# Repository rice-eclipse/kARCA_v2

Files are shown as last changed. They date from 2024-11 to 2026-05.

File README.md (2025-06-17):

# kARCA 2.0
kARCA 2.0 is a revision of [kARCA](https://github.com/rice-eclipse/karca):  Rice Eclipse's Engine Control System PCB for the data collection and remote control 
of their Titan II and Proxima Hybrid Rocket Motors

It performs the same functions as kARCA with the addition of thermocouple data collection, driver current monitoring, and battery monitoring.
In addition, various components have been replaced for updated ICs and the power regulation and load cell circuits have been revised.

A detailed description of the changes can be found on  [karca_v2/Docs/changelog](https://github.com/rice-eclipse/kARCA_v2/blob/main/karca_v2/Docs/kARCA_v2_Changelog.csv)

Detailed documentation on the circuit board can be found on [karca_v2/Docs/main_documentation](https://github.com/rice-eclipse/kARCA_v2/tree/main/karca_v2/Docs/karca_v2.md)

## Download and Usage
Download [KiCAD](https://www.kicad.org/download/)

Navigate to your preferred folder and clone into the repository:
```
git clone https://github.com/rice-eclipse/kARCA_v2.git
```
Open KiCAD and open the project file (.kicad_pro):
```
File > Open Project
```

Schematics: [karca_v2/Docs/Schematics](https://github.com/rice-eclipse/kARCA_v2/tree/main/karca_v2/Docs/Schematics)

Spice Simulations: [karca_v2/Docs/Simulations](https://github.com/rice-eclipse/kARCA_v2/tree/main/karca_v2/Docs/Simulations)

Board Files: [karca_v2/Docs/Board_Files](https://github.com/rice-eclipse/kARCA_v2/tree/main/karca_v2/Docs/Board_Files)

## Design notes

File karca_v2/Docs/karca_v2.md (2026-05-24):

# kARCA 2.0 Main Documentation

This document highlights the features and design choices of kARCA 2.0 as a reference for future work on the project.

## Project Overview
kARCA 2.0 is an engine control system  that is part of Rice Eclipse's Engine Testing Setup. The controller interfaces directly with the engine through the [controller software](https://github.com/rice-eclipse/mc-firmware), which runs on an STM32F207 nucleo board. The user interfaces with the controller using a frontend JavaScript dashboard `Quonkboard` from which they can visualize the data collected and send commands to actuate valves and start the ignition sequence.

**For future versions, it is recommended to upgrade to an STM32F429 for more RAM and a hardware FPU for efficient FIR filtering. The user can also use the STM32F407VET6 if a fully integrated solution is preferred (ie: MCU embedded on the main PCB)**
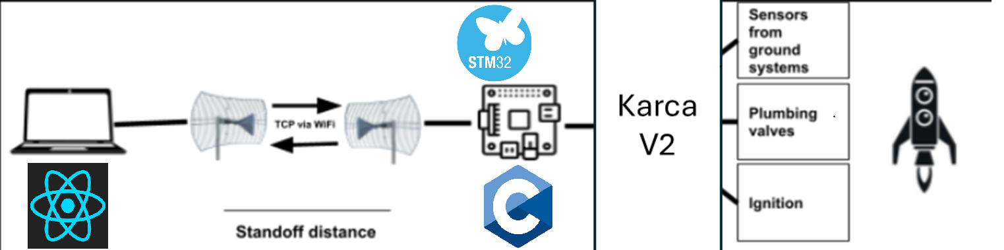
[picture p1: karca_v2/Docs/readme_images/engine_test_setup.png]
Engine Test Setup


## System Requirements
1. Collect data from 4 load cells, pressure transducers, and thermocouples at a 1kHz samplingfrequency
2. Control the 600W ignition system by driving an external two-stage relay
3. Control 5 valves, each drawing up to 1A of current at 12V
4. Monitor Battery voltage and current
5. Transmit real time data to the user

## Design Outline

### Power Distribution

The main power source is a 12V Lead-Acid Battery, which is spliit into 5V and 12V lines.

The 12V line is used for the drivers, ignition circuitry, and the pressure transducers.

The 5V line is used for the remaining ciruitry. The power conversion is performed by the [AP62300](https://www.diodes.com/assets/Datasheets/AP62300_AP62301_AP62300T.pdf) synchronous buck converter.

The battery current is monitored using a current shunt and a current sense amplifier. The voltage is monitored using a simple resistive divider circuit.

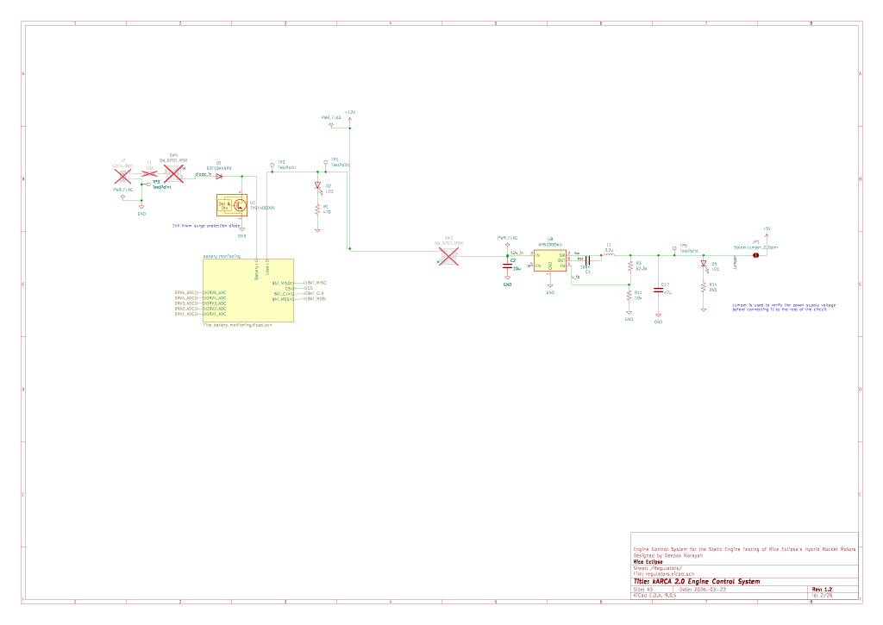
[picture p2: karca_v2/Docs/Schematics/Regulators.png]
Power Regulation

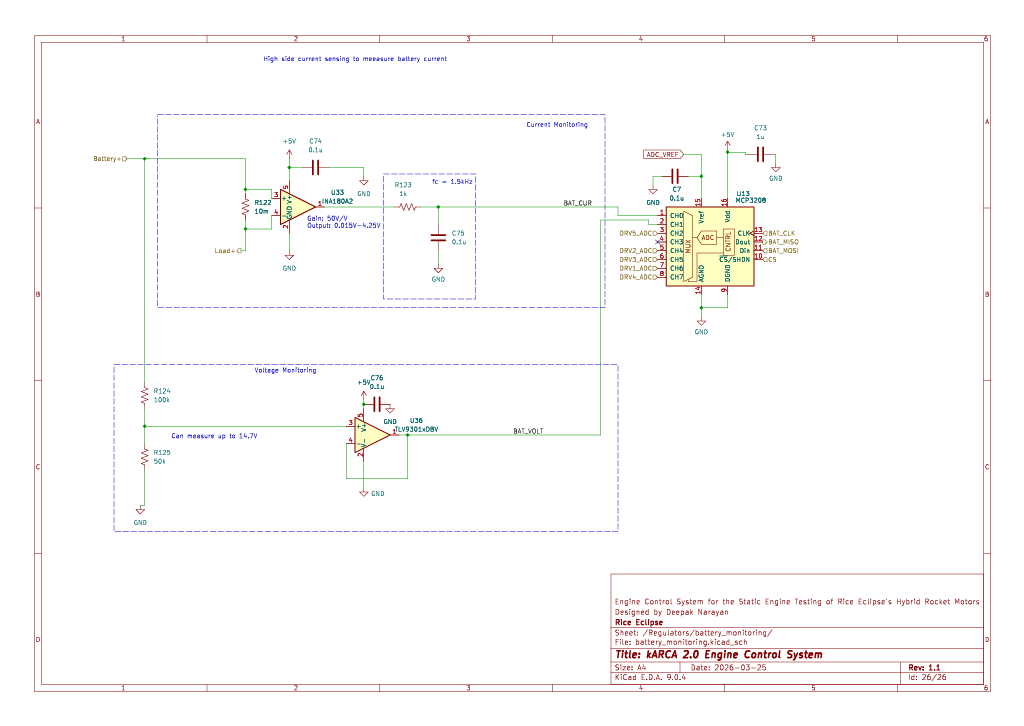
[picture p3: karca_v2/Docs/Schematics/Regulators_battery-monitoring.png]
Battery Monitoring


### Load Cell Data Collection
When supplied with an excitation voltage of 5V, the cell outputs a differential voltage proportonal to the applied force:
$$V_{dm} = \frac{V_{FSO}}{F_{FSO}}V_{DD}F$$
Where:
1. $V_{dm}$ is the output differential voltage
2. $V_{FSO}$ is the load cell's full scale voltage output: 3mV per volt of excitation when 3000lbf is applied
3. $V_{DD}$ is the exccitation voltage(5V in this case)
4. $F$ is the applied force

$V_{dm}$ is amplified using an instrumentation amplifier to obtain a single-ended readable signal (compatible with the ADC voltage resolution of 1.22mV). A two-pin jumper can be used to select the gain resistor connected to the instrumentation amplifier. A gain of 250 for the Titan load cell or a gain of 17 for the Proxima load cell can be chosen.

The single-ended signal is then filtered using a unity-gain active filter with a cutoff frequency of $1.5kHz$. This is to prevent aliasing during sampling.
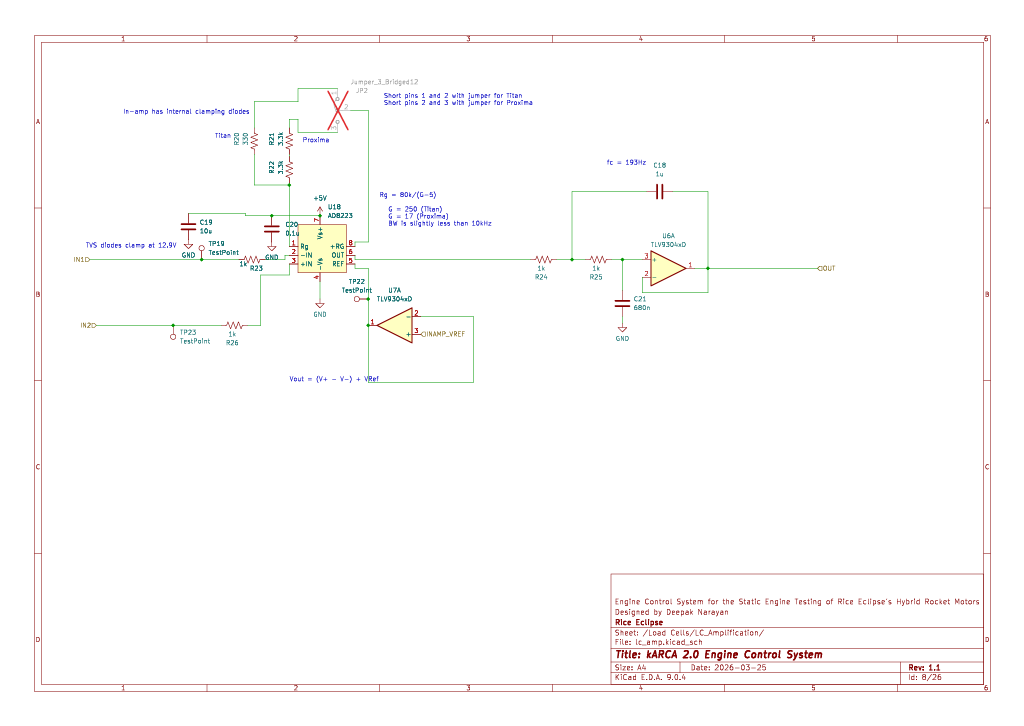
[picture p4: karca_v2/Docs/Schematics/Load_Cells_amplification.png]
Load Cell Amplification


### Pressure Transducer Data Collection
A pressure transducer is a 4-20mA device. It outputs a current that varies linearly with the measured pressure (4mA corresponds to 0 psig; 20mA corresponds to 1000psig). It usually consists of a wheatstone bridge circuit like a load cell and a current loop transmitter that converts the voltage to a current. The current signal provides stronger noise immunity. 

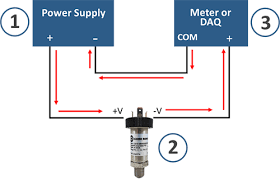
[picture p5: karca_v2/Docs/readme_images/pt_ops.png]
Pressure transducer circuit

The signal is converted back to a voltage using a $30\Omega$ shunt resistor. This results in a voltage range of 0.12V to 0.6V. A low shunt resistance is necessary to minimize the voltage drop as the pressure transducers need a minimum of 8V to operate.

The signal is amplified with a gain of 8 using an active filter with a cutoff frequency of $193Hz$. Therefore the full voltage range is from 0.96V to 4.8V, corresponding to a resolution of 0.31psi.

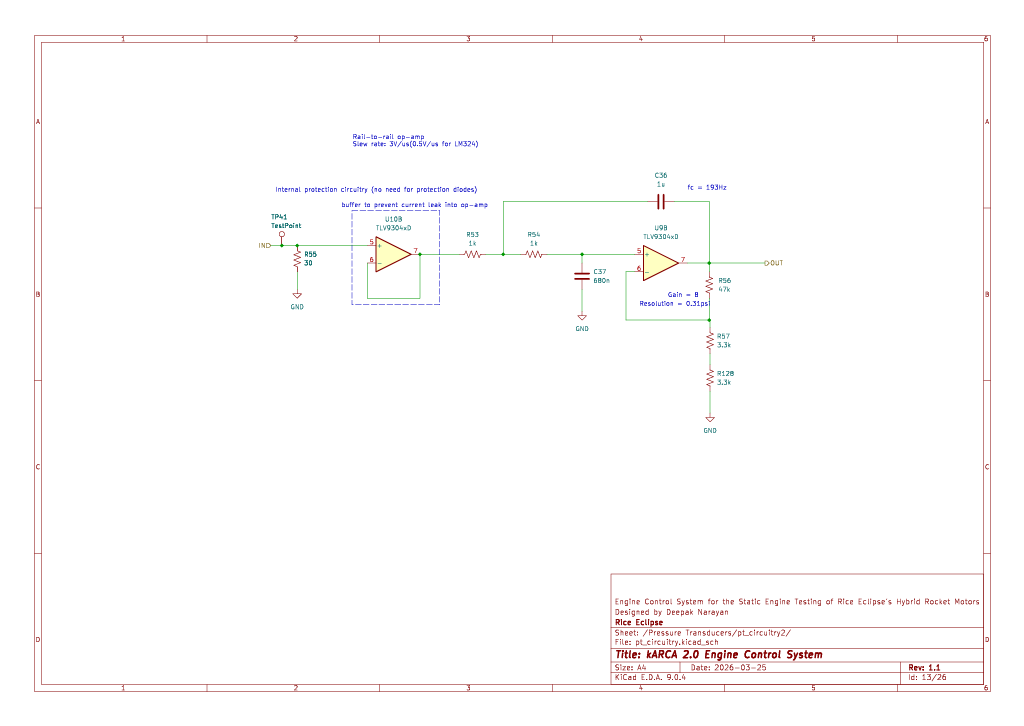
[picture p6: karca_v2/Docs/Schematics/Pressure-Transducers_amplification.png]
Pressure Transducer Amplification


### Thermocouple Data Collection
Thermocouples output a very small voltage signal that is proportional to the temperature difference between the measurement junction and a reference junction.
 ($5mV/^{\\circ}C$). This differential signal is amplified by the AD8495 Thermocouple amplifier with a gain of 122.4. The output voltage is thus:
 $$V_{out} = (T_{measured}\cdot mV/^{\\circ}C)\cdot 122.4$$

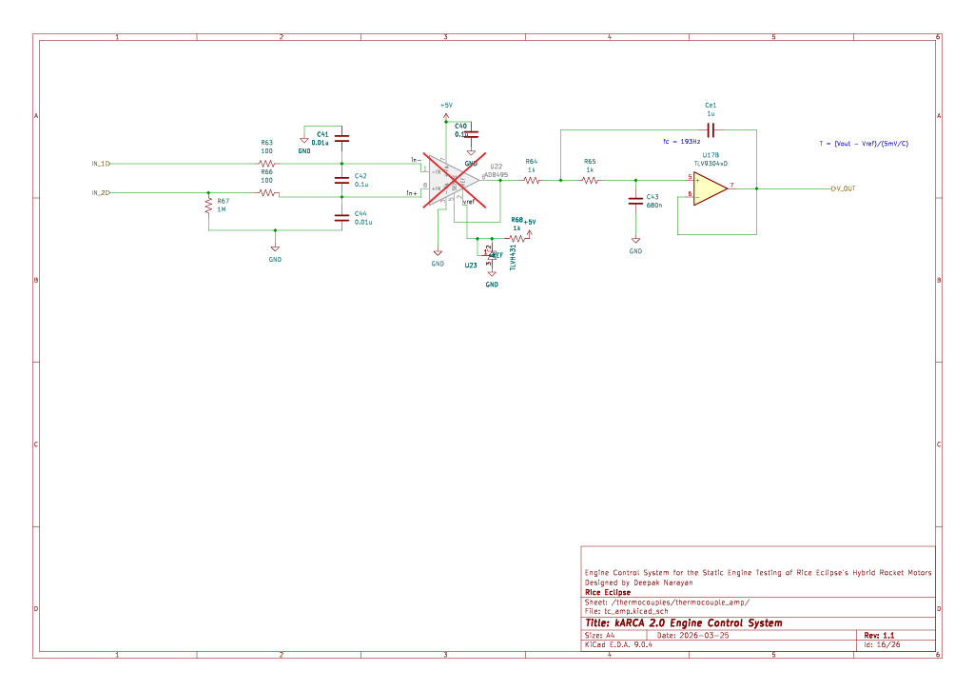
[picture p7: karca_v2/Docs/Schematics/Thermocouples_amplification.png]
Thermocouple Amplification
 

### Analog-to-Digital Conversion and Processing
The analog signals from the thermocouple, load cell, and pressure transducer conditioning circuits are input to two [MCP3208](https://www.microchip.com/en-us/product/mcp3208) 12-bit ADCs. The driver current and battery monitoring circuit outputs are input to a third MCP3208 ADC. The outputs from the first two ADCs are sent to the microcontroller over an SPI bus. The output from the third ADC is sent to the microcontroller over another SPI bus. This allows for a faster sample rate as there are fewer channel scans needed for each sampling cycle.

These ADCs have a Signal to Noise and Distortion (SINAD) of 72dB, providing an ENOB of ~11.

**For future revisions, it is recommended to use the internal ADCs as these allow for easy channel scanning and DMA transactions**
 ### Valve Actuation
 Each valve is driven by the AO3400 mosfet. These mosfets have a very low $$R_{DS,on}$$, allowing sufficient current to flow when then gate is driven by 3.3V from the 
 STM32F207 GPIO. There are also green status LEDs that light up, when a valve is actuated.

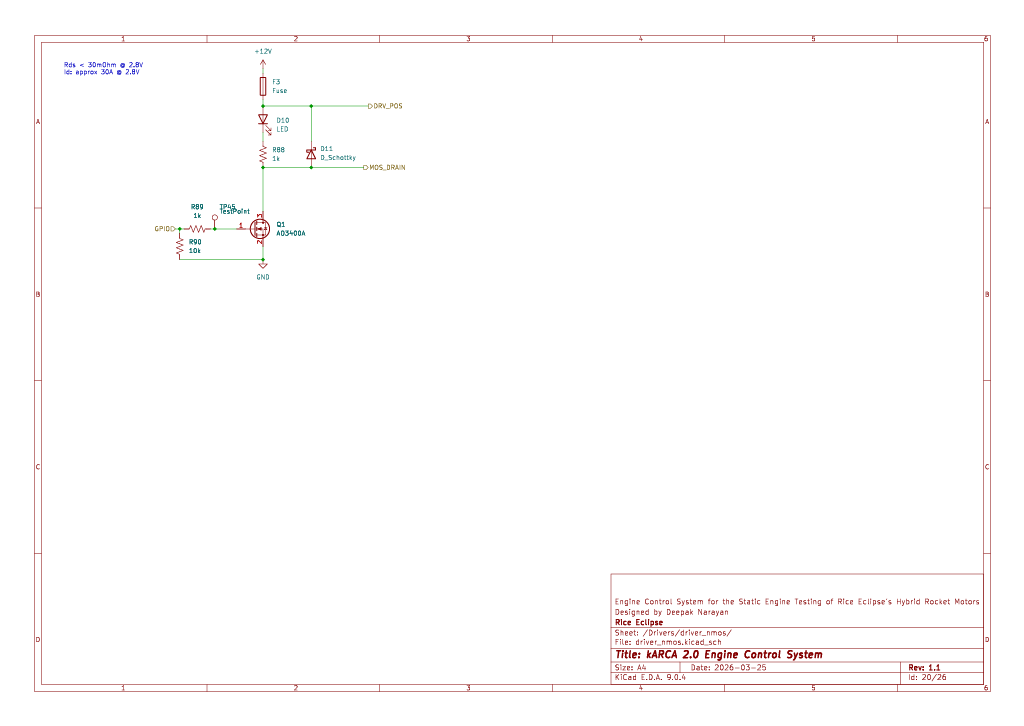
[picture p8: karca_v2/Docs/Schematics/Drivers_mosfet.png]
Driver Schematics
 

 To ensure that the valve actuates when the driver is turned on, the current through the valve is measured using current sense amplifiers and shunt resistors.
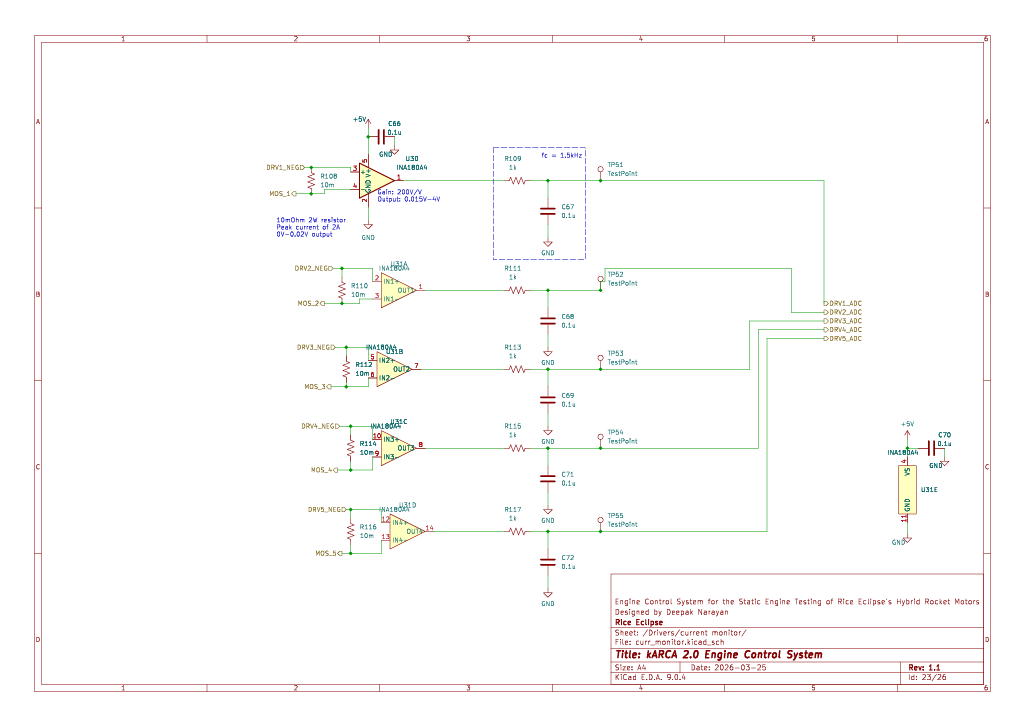
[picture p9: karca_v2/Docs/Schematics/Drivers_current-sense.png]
Driver Current Sense
 

 ### Board Layout
 The board is 25cm x 14.5cm since space wasn't a major concern. Components were grouped according to their function and were spaced out since being able to modify traces and easily replace components by hand were priorities.

 The board consists of 4 layers: SIGNAL-GND-PWR-SIGNAL. This keeps the signal traces close to a reference plane. The power plane is much simpler than that of the original kARCA design; it only consists of a single 5V plane and the 12V is supplied using traces. This prevents potential signal deterioration due to signals crossing split power planes.

 All the components are mounted on the top layer.

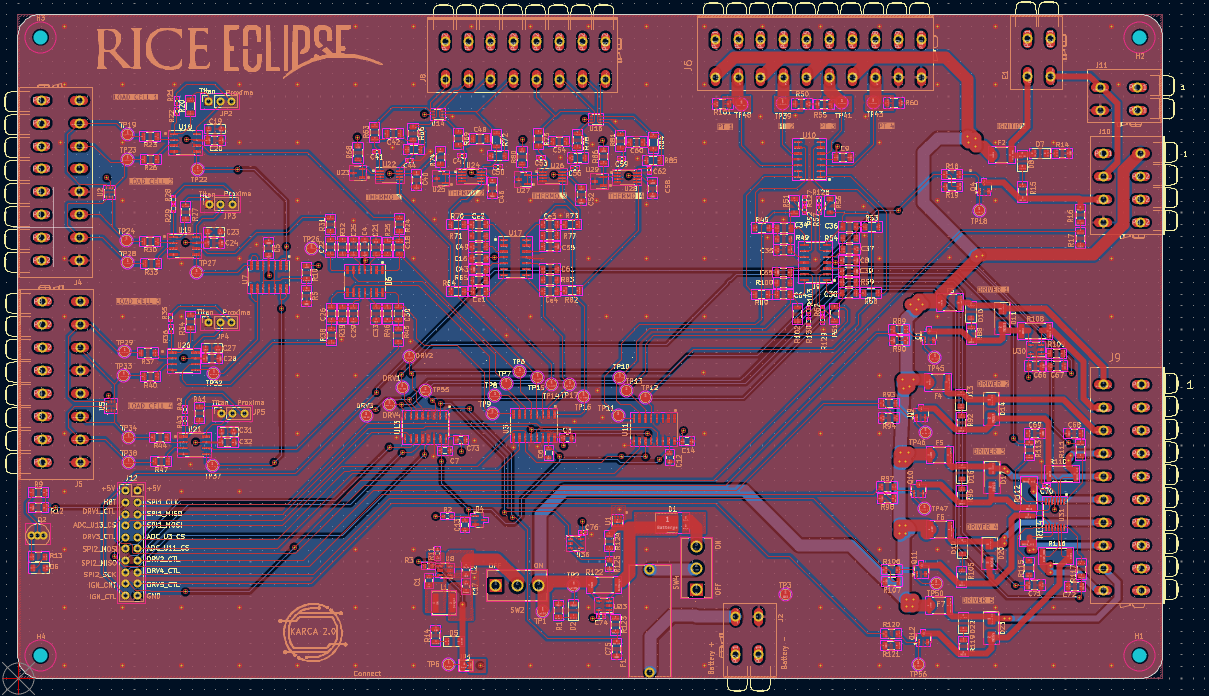
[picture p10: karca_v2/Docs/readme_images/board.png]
Karca
 
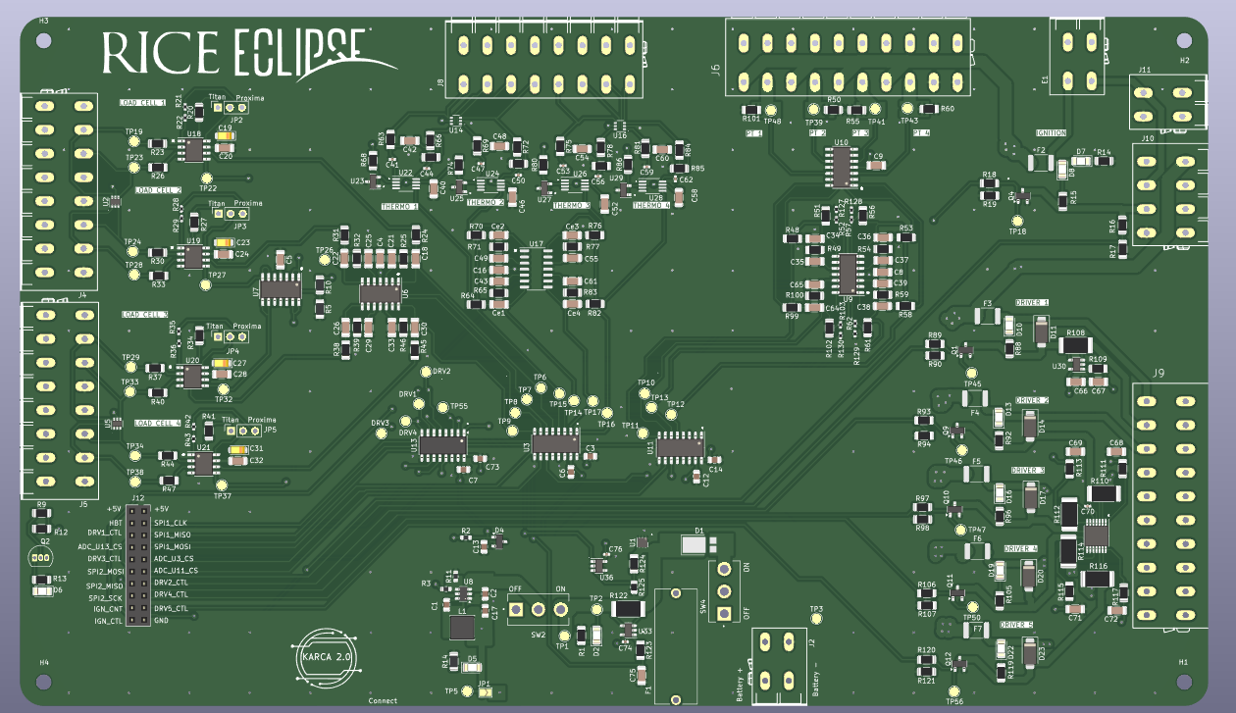
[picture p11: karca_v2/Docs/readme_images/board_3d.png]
Karca 3D


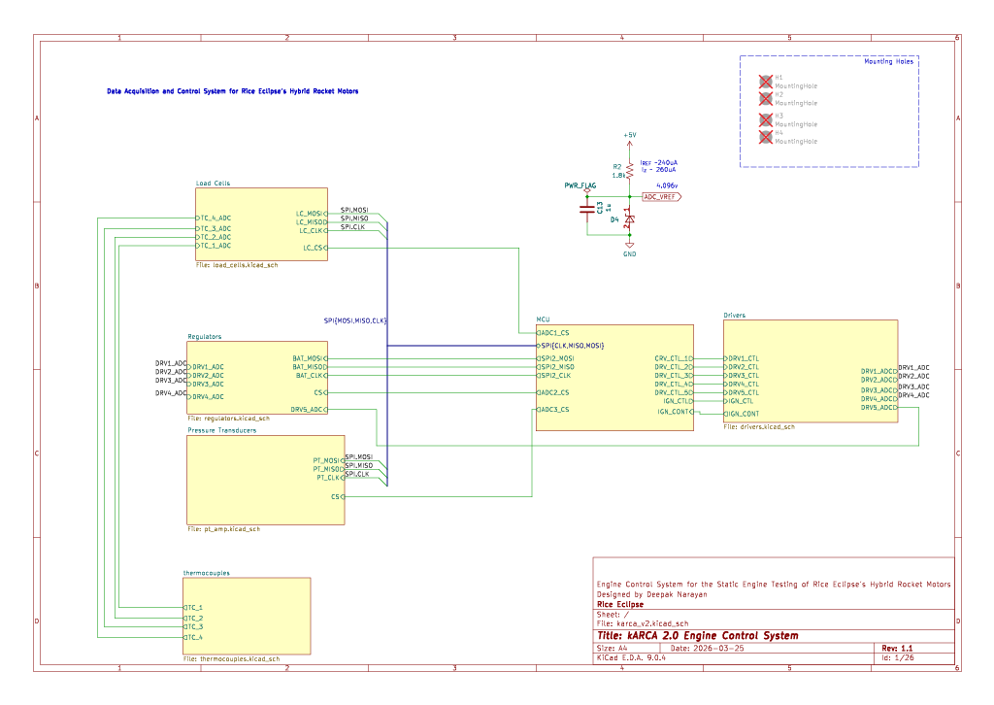
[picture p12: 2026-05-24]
karca_v2/Docs/Schematics/Main.png

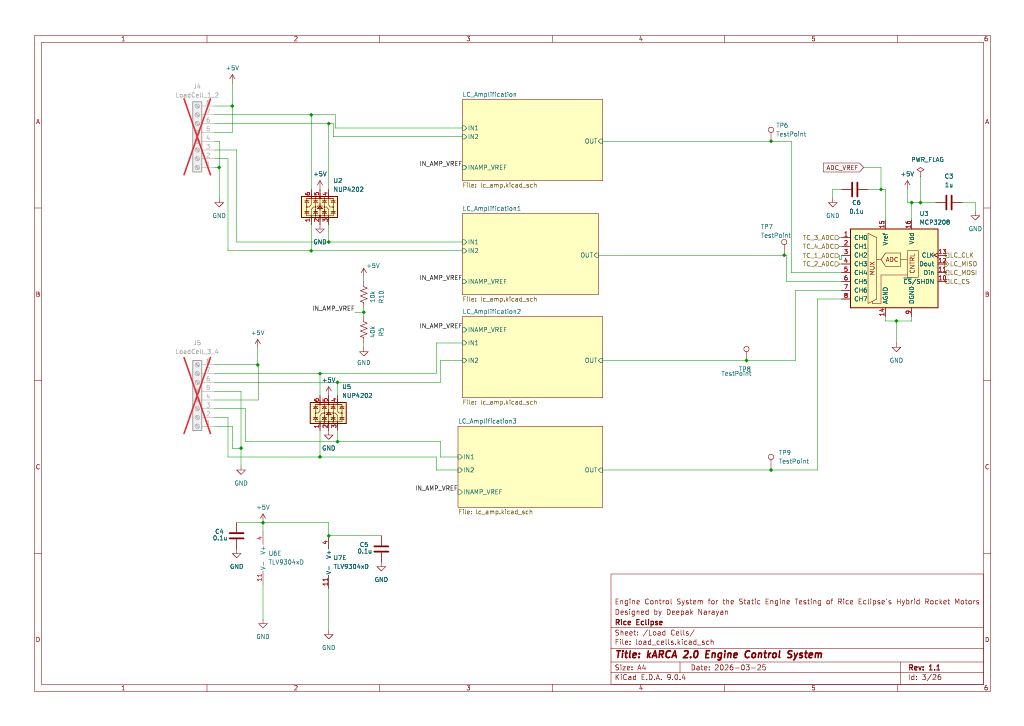
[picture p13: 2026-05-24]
karca_v2/Docs/Schematics/Load-Cells.png

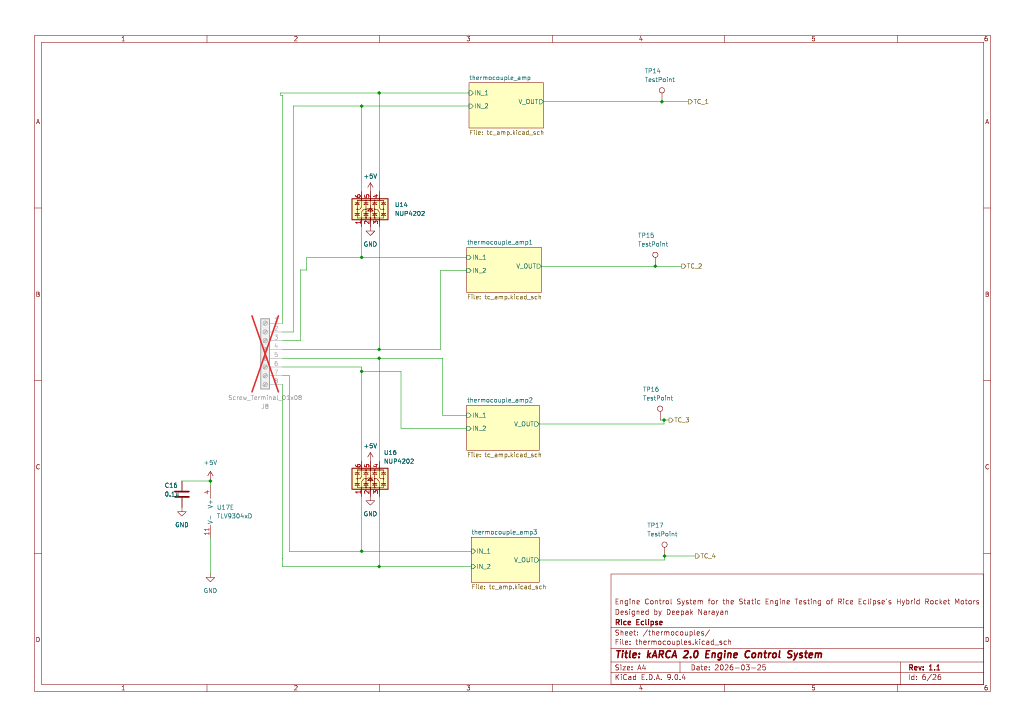
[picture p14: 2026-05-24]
karca_v2/Docs/Schematics/Thermocouples.png

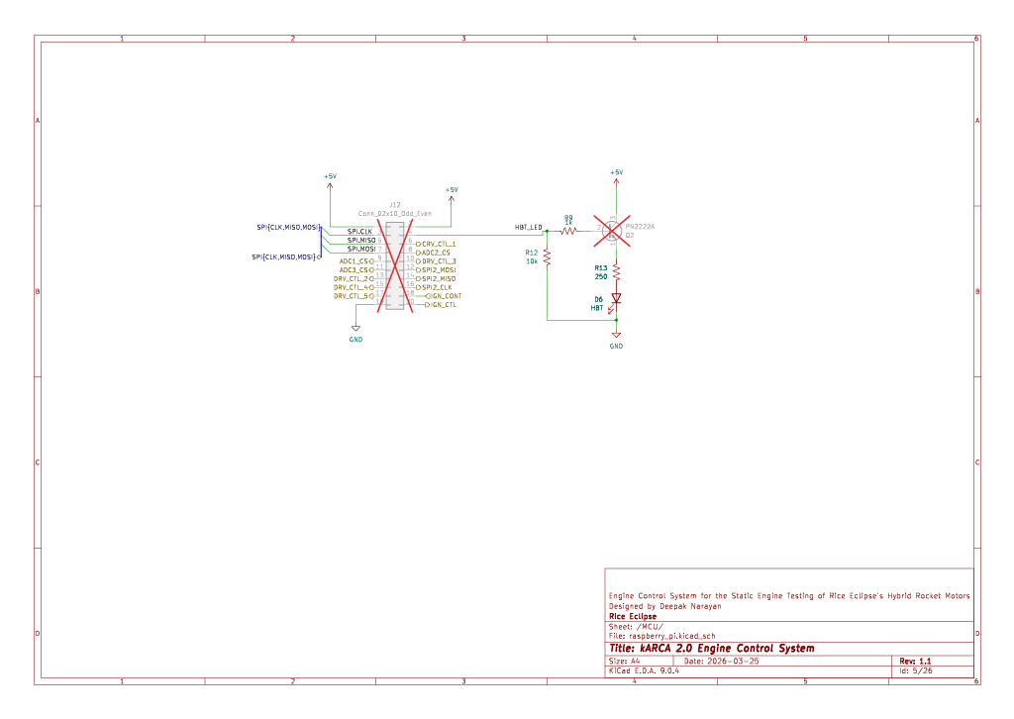
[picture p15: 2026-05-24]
karca_v2/Docs/Schematics/mcu.png

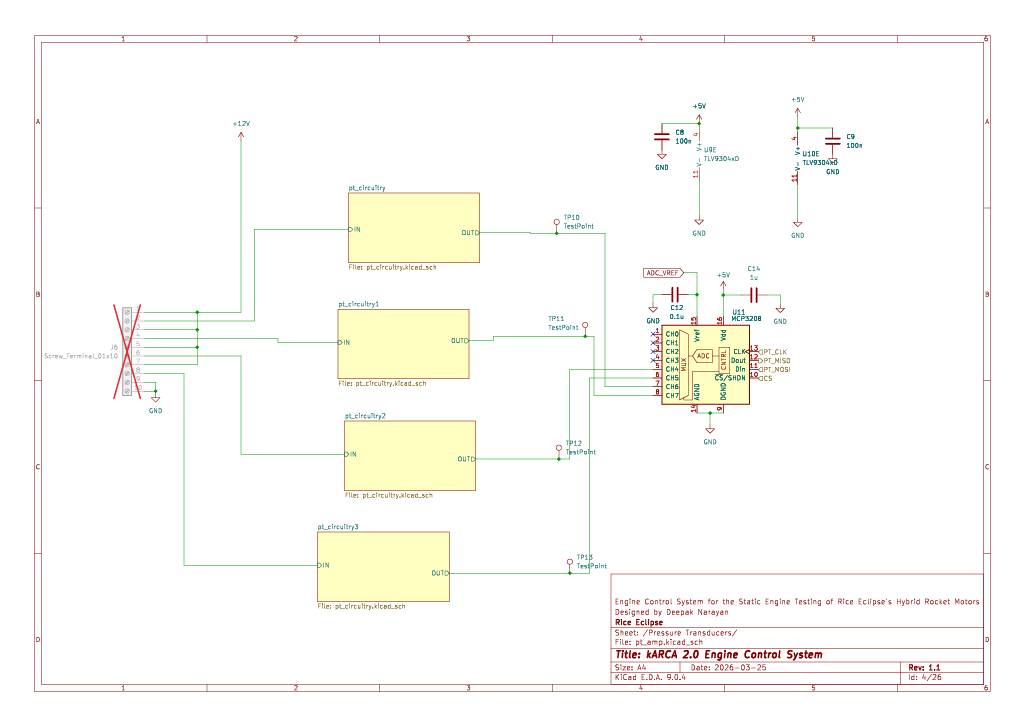
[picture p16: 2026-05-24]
karca_v2/Docs/Schematics/Pressure-Transducers.png

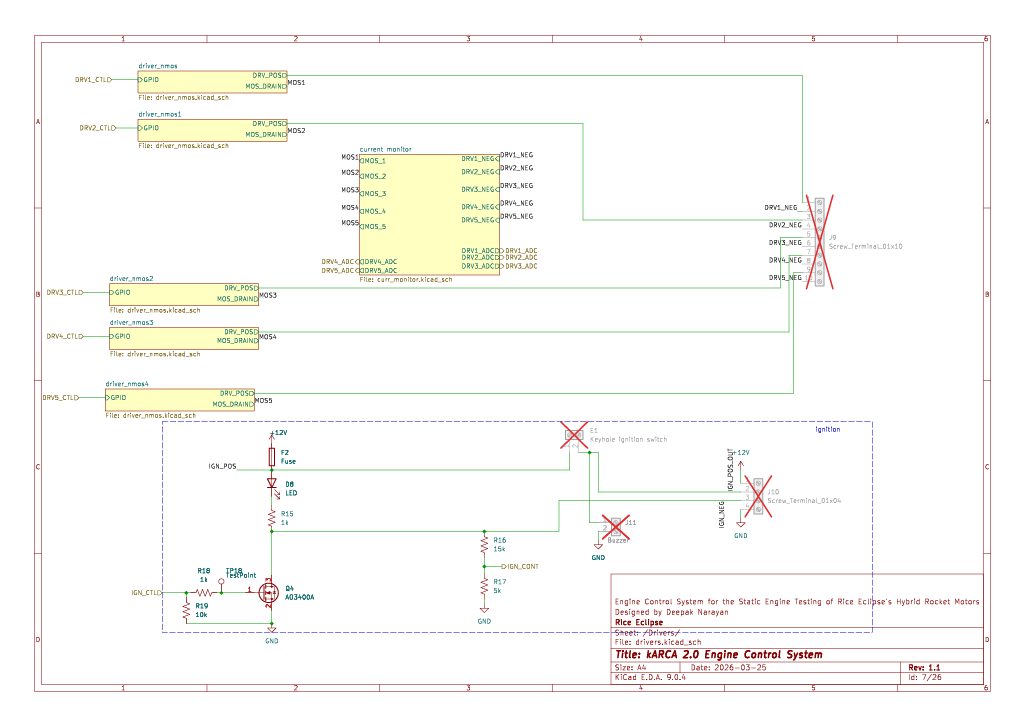
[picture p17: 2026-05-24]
karca_v2/Docs/Schematics/Drivers.png

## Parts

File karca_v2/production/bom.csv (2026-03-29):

Designator | Footprint | Quantity | Value | LCSC Part #
C1 | 0805 | 1 | 100n | C28233
C12, C6 | 0805 | 2 | 0.1u | C28233
C13, C73 | 0805 | 2 | 1u | C28323
C14, C3 | 0805 | 2 | 1u | C28323
C16, C20, C24, C28, C32, C4, C40, C42, C46, C48, C52, C54, C58, C60, C66, C67, C68, C69, C71, C72 | 1206 | 20 | 0.1u | C24497
C17 | 0805 | 1 | 47u | C16780
C18, C22, C26, C30, C34, C36, C38, C64, CE1, CE2, CE3, CE4 | 1206 | 12 | 1u | C1848
C19, C23, C27, C31 | CP_EIA-3216-18_Kemet-A | 4 | 10u | C110052
C2 | 0805 | 1 | 10u | C15850
C21, C25, C29, C33 | 1206 | 4 | 680n | C1881
C35, C37, C39, C43, C49, C55, C61, C65 | 1206 | 8 | 680n | C1881
C41, C47, C53, C59 | 0402 | 4 | 0.01u | C15195
C44, C50, C56, C62 | 0402 | 4 | 0.01u | C15195
C5 | 1206 | 1 | 0.1u | C24497
C7 | 0805 | 1 | 0.1u | C28233
C70 | 0402 | 1 | 0.1u | C1525
C74, C76 | 0402 | 2 | 0.1u | C1525
C75 | 1206 | 1 | 0.1u | C24497
C8, C9 | 1206 | 2 | 100n | C24497
D1 | D_PowerDI-5 | 1 | SDT10A45P5 | C2759901
D10, D13, D16, D19, D22, D8 | 1206 | 6 | LED | C14641
D11, D14, D17, D20, D23 | D_SMA | 5 | D_Schottky | C7428238
D2, D5 | 1206 | 2 | LED | C2298
D4 | SOT-23 | 1 | LM4040DBZ-4.1 | C126807
D6 | 1206 | 1 | HBT | C2298
D7 | 1206 | 1 | LED | C125084
F2 | 1812 | 1 | Fuse | C55996
F3, F4, F5, F6, F7 | 1812 | 5 | Fuse | C21010
L1 | L_Sunlord_SWPA5040S | 1 | 3.3u | C305173
Q1, Q10, Q11, Q12, Q9 | SOT-23 | 5 | AO3400A | C20917
Q4 | SOT-23 | 1 | AO3400A | C20917
R1 | 1206 | 1 | 470 | C4502
R10, R19 | 1206 | 2 | 10k | C1489
R100, R109, R111, R113, R115, R117, R14_2, R15, R18, R23, R24, R25, R26, R30, R31, R32, R33, R37, R38, R39, R40, R44, R45, R46, R47, R48, R49, R53, R54, R58, R59, R64, R65, R68, R70, R71, R74, R76, R77, R80, R82, R83, R86, R99 | 1206 | 44 | 1k | C104594
R101, R50, R55, R60 | 1206 | 4 | 30 | C17886
R102, R51, R56, R61 | 1206 | 4 | 47k | C25664
R103, R52, R57, R62 | 0402 | 4 | 3.3k | C26032
R105, R106, R119, R120, R88, R89, R92, R93, R96, R97 | 1206 | 10 | 1k | C104594
R107, R121, R90, R94, R98 | 1206 | 5 | 10k | C1489
R108, R110, R112, R114, R116 | 2512 | 5 | 10m | C105142
R11 | 0603 | 1 | 10k | C15401
R12 | 1206 | 1 | 10k | C17902
R122 | 2512 | 1 | 10m | C105142
R123, R9 | 1206 | 2 | 1k | C4410
R124 | 1206 | 1 | 100k | C17900
R125 | 0805 | 1 | 50k | C316211
R127, R128, R129, R130, R22, R29, R36, R43 | 0402 | 8 | 3.3k | C25890
R13 | 1206 | 1 | 250 | C2828898
R14 | 1206 | 1 | 250 | C2828898
R16 | 1206 | 1 | 15k | C1493
R17 | 1206 | 1 | 5k | C872846
R2 | 0603 | 1 | 1.8k | C4177
R20, R27, R34, R41 | 1206 | 4 | 330 | C17930
R21, R28, R35, R42 | 0402 | 4 | 3.3k | C25890
R3 | 0603 | 1 | 52.3k | C185323
R5 | 1206 | 1 | 40k | C870723
R63, R69, R75, R81 | 1206 | 4 | 100 | C17901
R66, R72, R78, R84 | 1206 | 4 | 100 | C17901
R67, R73, R79, R85 | 1206 | 4 | 1M | C17927
U1 | WSON-6-1EP_2x2mm_P0.65mm_EP1x1.6mm | 1 | TVS1400DRV | C1975229
U10, U17, U6, U9 | SO-14_3.9x8.65mm_P1.27mm | 4 | TLV9304xD | C2873295
U11, U3 | SOIC-16_3.9x9.9mm_P1.27mm | 2 | MCP3208 | C16939
U13 | SOIC-16_3.9x9.9mm_P1.27mm | 1 | MCP3208 | C16939
U14, U16 | SOT-363_SC-70-6 | 2 | NUP4202 | C2937014
U18, U19, U20, U21 | SOIC-8_3.9x4.9mm_P1.27mm | 4 | AD8223 | C1346337
U2, U5 | SOT-363_SC-70-6 | 2 | NUP4202 | C2937014
U23, U25, U27, U29 | SOT-23 | 4 | TLVH431 | C2156609
U30 | SOT-23-5 | 1 | INA180A4 | C133969
U31 | TSSOP-14_4.4x5mm_P0.65mm | 1 | INA180A4 | C2058313
U33 | SOT-23-5 | 1 | INA180A2 | C116203
U36 | SOT-23-5 | 1 | TLV9301xDBV | C4366617
U7 | SO-14_3.9x8.65mm_P1.27mm | 1 | TLV9304xD | C2873295
U8 | TSOT-23-6 | 1 | AP62300WU | C1880390

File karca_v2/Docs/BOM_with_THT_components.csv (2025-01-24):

Comment | Designator | Link | Price per unit | Units | Total Price | Status
P-2604-1102 | J1,J2, J11, E1 |  |  |  |  |  | Arrived
P-2604-1104 | J10 |  |  |  |  |  | Purchased
P-2604-1108 | J4,J5,J8 |  |  |  |  |  | Not yet purchased
P-2604-1110 | J6 |  |  |  |  |  | Not purchasing
Micro USB-B Molex-1050171001 | J3 | link | 1.48 | 2
OKL-T6_W12N-C | MD1 | link | 9.27 | 1
10A Fuse:4628 | F1 | link | 0.81 | 2
Diode: 90SQ035: DO-201AD | D1 | link | 0.94 | 2
headers (P=2.00mm) | JP1,JP2,JP3,JP4,JP5, J7 | LINK | 0.48 | 5
PN2222A (TO-92) | Q2
IRF3708 (TO-220-3) | Q3, Q4, Q5, Q6, Q7, Q8 | LINK | 7.69 | 10
30k potentiometer (Bourns_3296W_Vertical) | RV1 | link | 2.47 | 1
500SSP1S2M2QEA SPST Switch | SW1, SW2, SW3 | link | 5.3 | 3

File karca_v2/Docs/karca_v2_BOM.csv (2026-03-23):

Comment | Designator | Footprint | LCSC Part Number
10uF | C1, C19, C23, C27, C31 | 1206 | C13585 | 5 | 258
10uF | C2, C10, C11 | 1206 | C13585 | 3
0.1uF | C3, C4, C5, C16, C18, C20, C21, C22, C24, C25, C26, C28, C29, C30, C32, C33, C34, C35, C36, C37, C38, C39, C40, C42, C43, C46, C48, C49, C52, C54, C55, C58, C60, C61, C64, C65, C66, C67, C68, C69, C70, C71, C72, C73, C74, C75, C76, Ce1, Ce2, Ce3, Ce4 | 1206 | C24497 | 51
100nF | C8, C9, C14 | 1206 | C24497 | 3
1uF | C15 | 1206 | C1848 | 1
0.01uF | C41, C44, C47, C50, C53, C56, C59, C62 | 0402 | C15195 | 8
LED Orange | D7, D9, D12, D15, D18, D21 | 1206 | C183851 | 6
LED Green | D2, D3, D4, D8, D10, D13, D16,D19, D22 | 1206 | C14641 | 9
D_Schottky | D5, D11, D14, D17, D20, D23 | SMA(DO-214AC) | C2480 | 6
HBT LED Red | D6 | 1206 | C125086 | 1
Fuse | F2, F3, F4, F5, F6, F7 | 1812 | C20814 | 6
OKL-T_6-W12N-C | MD1 | MURATA_OKL-T-6-W12N-C_0 | C6248591 | 1
AO3401A | Q1 | SOT23 | C15127 | 1
470R | R1 | 1206 | C4502 | 1
10kR | R2, R10, R11, R12, R19, R90, R94, R98, R107, R121 | 1206 | C17902 | 10
250R | R3, R5, R6, R13 | 1206 | C2828898 | 4
10MR | R7 | 1206 | C26119 | 1
1.15MR | R8 | 1206 | C332934 | 1
1kR | R4, R9, R14, R15, R18, R23, R24, R25, R26, R30, R31, R32, R33, R37, R38, R39, R40, R44, R45, R46, R47, R48, R49, R53, R54, R58, R59, R64, R65, R68, R70, R71, R74, R76, R77, R80, R82, R83, R86, R87, R88, R89, R91, R92, R93, R95, R96, R97, R99, R100, R104, R105, R106, R109, R111, R113, R115, R117, R118, R119, R120, R123 | 1206 | C4410 | 62
15kR | R16 | 1206 | C25828 | 1
5kR | R17 | 1206 | C870818 | 1
330R | R20, R27, R34, R41, R126 | 1206 | C104769 | 5
3.3kR | R21, R22, R28, R29, R35, R36, R42, R43 | 0402 | C25890 | 8
30R | R50, R55, R60, R101 | 1206 | C25373 | 4
47kR | R51, R56, R61, R102 | 1206 | C25664 | 4
3.3kR | R52, R57, R62, R103, R127, R128, R129, R130 | 0402 | C149918 | 8
100R | R63, R66, R69, R72, R75, R78, R81, R84 | 1206 | C17901 | 8
1MR | R67, R73, R79, R85 | 1206 | C17927 | 4
10mR | R108, R110, R112, R114, R116, R122 | 2512 | C241862 | 6
100kR | R124 | 1206 | C17900 | 1
50kR | R125 | 0805 | C316211 | 1
TVS1400DRV | U1 | WSON-6-1EP_2x2mm | C1975229 | 1
NUP4202 | U2, U4, U5, U12, U32, U35 | SOT-363 | C89319 | 6
MCP3208 | U3, U11 | SOIC-16 | C16939 | 2
TLV9304xD | U6, U7, U9, U10 | SOIC-14 | C2873295 | 4
TPS7A24 | U8 | SOT-23-5 | C2693328 | 1
AD8223 | U18, U19, U20, U21 | SOIC-8 | C652531 | 4
TLVH431BIL3T | U23, U25, U27, U29 | SOT-23 | C1852785 | 4
INA180A4 | U30 | SOT-23-5 | C133969 | 1
INA4180A4 | U31 | TSSOP-14 | C2058313 | 1
INA180A2 | U33 | SOT-23-5 | C192764 | 1
MCP3204 | U34 | SOIC-14 | C32816 | 1
TLV9301xDBV | U36 | SOT-23-5 | C2867945 | 1
 |  |  |  | 258

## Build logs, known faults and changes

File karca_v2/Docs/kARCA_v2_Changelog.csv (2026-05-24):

Version 2.1 changes
"reorganized ADC arrangement  (LCs + TCs, PTs, Monitoring)"
Added dedicated vref for the adcs
Reduced cutoff frequency to 200Hz
Removed extra status leds for mosfets
Fixed vref for IN-AMPS with fixed resistors
Replaced OKW-T/6-W12N power module with AP62300 DC-DC
Replaced IRF3708 NMOS with AO3400A NMOS
Added secondary SPI bus for driver current monitoring and battery monitoring

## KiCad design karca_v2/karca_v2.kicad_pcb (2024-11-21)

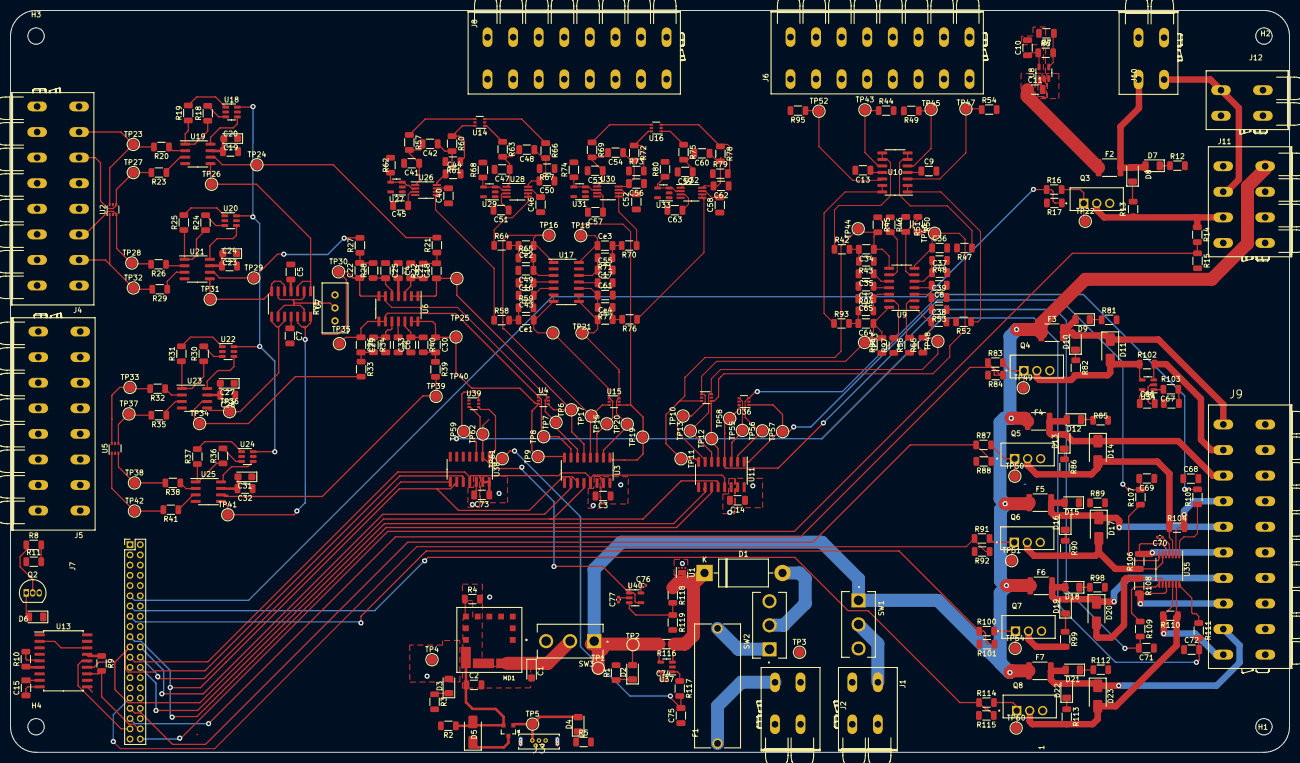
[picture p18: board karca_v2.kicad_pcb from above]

Board: 4 copper layers, 250.0 x 145.0 mm, 361 parts (0 on the bottom side), 199 nets.

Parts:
C1, C19, C23, C27, C31: 10u; CP_EIA-3216-18_Kemet-A
C2, C10, C11: 10u; C_1206_3216Metric
C3, C4, C5, C6, C7, C16, C17, C20, C24, C28, C32, C40, C42, C45, C46, C48, C51, C52, C54, C57, C58, C60, C63, C66, C67, C68, C69, C71, C72, C73, C75: 0.1u; C_1206_3216Metric
C8, C9, C12, C13, C14: 100n; C_1206_3216Metric
C15: 1u; C_1206_3216Metric
C18, C22, C26, C30, C34, C36, C38, C64: 0.15u; C_1206_3216Metric
C21, C25, C29, C33, C35, C37, C39, C43, C49, C55, C61, C65: 0.075u; C_1206_3216Metric
C41, C44, C47, C50, C53, C56, C59, C62: 0.01u; C_1206_3216Metric
C70, C74, C76, C77: 0.1u; C_0402_1005Metric
Ce1, Ce2, Ce3, Ce4: 0.15u; C_1206_3216Metric
D1: 1N5822RLG; D_DO-201AD_P15.24mm_Horizontal
D2, D3, D4, D7, D8, D9, D10, D12, D13, D15, D16, D18, D19, D21, D22: LED; LED_1206_3216Metric
D5, D11, D14, D17, D20, D23: D_Schottky; D_SMA
D6: HBT; LED_1206_3216Metric
F1: 10A; FUSE_4628
F2, F3, F4, F5, F6, F7: Fuse; Fuse_1812_4532Metric
H1, H2, H3, H4: MountingHole; MountingHole_3.2mm_M3
J1: CON_FAN1; P-2604-1102
J2: Conn_Batt; P-2604-1102
J3: USB_B_Micro; GCT_USB3130-XX-X_REVD
J4: LoadCell_1_2; P-2604-1108
J5: LoadCell_3_4; P-2604-1108
J6, J8: Screw_Terminal_01x08; P-2604-1108
J7: Raspberry_pi; PinHeader_2x20_P2.00mm_Vertical
J9: Screw_Terminal_01x10; P-2604-1110
J10: Keyhole ignition switch; P-2604-1102
J11: Screw_Terminal_01x04; P-2604-1104
J12: Buzzer; P-2604-1102
MD1: OKL-T_6-W12N-C; MURATA_OKL-T-6-W12N-C_0
Q1: AO3401A; SOT23-3
Q2: PN2222A; TO-92_Inline
Q3, Q4, Q5, Q6, Q7, Q8: IRF3708; TO254P1041X444X1930-3
R1: 470; R_1206_3216Metric
R2, R9, R10, R11, R17, R84, R88, R92, R101, R115: 10k; R_1206_3216Metric
R3, R5: 250; R_1206_3216Metric
R4: 1.34k; R_1206_3216Metric
R6: 10.4M; R_1206_3216Metric
R7: 1.2M; R_1206_3216Metric
R8, R12, R13, R16, R20, R21, R22, R23, R26, R27, R28, R29, R32, R33, R34, R35, R38, R39, R40, R41, R42, R43, R47, R48, R52, R53, R58, R59, R62, R64, R65, R68, R70, R71, R74, R76, R77, R80, R81, R82, R83, R85, R86, R87, R89, R90, R91, R93, R94, R98, R99, R100, R103, R105, R107, R109, R111, R112, R113, R114, R117: 1k; R_1206_3216Metric
R14: 15k; R_1206_3216Metric
R15: 5k; R_1206_3216Metric
R18, R24, R30, R36: 330; R_1206_3216Metric
R19, R25, R31, R37, R46, R51, R56, R97: 6.7k; R_1206_3216Metric
R44, R49, R54, R95: 30; R_1206_3216Metric
R45, R50, R55, R96: 47k; R_1206_3216Metric
R57, R60, R63, R66, R69, R72, R75, R78: 100; R_1206_3216Metric
R61, R67, R73, R79: 1M; R_1206_3216Metric
R102, R104, R106, R108, R110, R116: 10m; R_1206_3216Metric
R118: 100k; R_1206_3216Metric
R119: 50k; R_1206_3216Metric
RV1: 30k; Potentiometer_Bourns_3296W_Vertical
SW1, SW2, SW3: SW_SPST; SW_500SSP1S2M2QEA
TP1, TP2, TP3, TP4, TP5, TP6, TP7, TP8, TP9, TP10, TP11, TP12, TP13, TP14, TP15, TP16, TP17, TP18, TP19, TP20, TP21, TP22, TP23, TP24, TP25, TP26, TP27, TP28, TP29, TP30, TP31, TP32, TP33, TP34, TP35, TP36, TP37, TP38, TP39, TP40, TP41, TP42, TP43, TP44, TP45, TP46, TP47, TP48, TP49, TP50, TP51, TP52, TP53, TP54, TP55, TP56, TP57, TP58, TP59, TP60, TP61, TP62: TestPoint; TestPoint_Pad_D2.0mm
U1: TVS1400DRV; WSON-6-1EP_2x2mm_P0.65mm_EP1x1.6mm
U2, U4, U5, U12, U14, U15, U16, U36, U39: NUP4202; SOT-363_SC-70-6
U3, U11: MCP3208; SOIC-16_3.9x9.9mm_P1.27mm
U6, U7, U9, U10, U17: TLV9304xD; SO-14_3.9x8.65mm_P1.27mm
U8: TPS7A24; SOT-23-5
U13: M41T93; SOIC-18W_7.5x11.6mm_P1.27mm
U18, U20, U22, U24: TS5A3159ADBVR; SOT-23-6
U19, U21, U23, U25: AD8223; SOIC-8_3.9x4.9mm_P1.27mm
U26, U28, U30, U32: AD8495; MSOP-8_3x3mm_P0.65mm
U27, U29, U31, U33: SOT-23-5
U34: INA180A4; SOT-23-5
U35: TSSOP-14_4.4x5mm_P0.65mm
U37: INA180A2; SOT-23-5
U38: MCP3204; SO-14_3.9x8.65mm_P1.27mm
U40: TLV9301xDBV; SOT-23-5

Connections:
+5V: C2.1, C3.1, C4.2, C5.2, C8.2, C9.1, C14.1, C16.2, C19.2, C20.2, C23.2, C24.2, C27.2, C28.2, C31.2, C32.2, C40.2, C46.2, C52.2, C58.2, C66.1, C70.1, C73.1, C74.1, C76.1, D3.2 (A), D5.1 (K), D5.2 (A), J4.1, J4.5, J7.2, J7.4, MD1.4 (VOUT), Q1.2 (G), Q1.3 (S), Q2.3 (C), R2.1, R9.1, R10.1, R62.2, R68.2, R74.2, R80.2, RV1.3, TP4.1, U2.5, U3.15 (Vref), U3.16 (Vdd), U4.5, U5.5, U6.4 (V+), U7.4 (V+), U9.4 (V+), U10.4 (V+), U11.15 (Vref), U11.16 (Vdd), U12.5, U13.6 (DU), U13.15 (VCC), U14.5, U15.5, U16.5, U17.4 (V+), U18.5 (V+), U19.7 (Vs+), U20.5 (V+), U21.7 (Vs+), U22.5 (V+), U23.7 (Vs+), U24.5 (V+), U25.7 (Vs+), U26.7 (+Vs), U28.7 (+Vs), U30.7 (+Vs), U32.7 (+Vs), U34.5 (V+), U35.4 (VS), U36.5, U37.5 (V+), U38.13 (Vref), U38.14 (Vdd), U39.5, U40.5 (V+)
+12V: C11.1, D2.2 (A), F2.1, F3.1, F4.1, F5.1, F6.1, F7.1, J11.1, R116.2, SW1.1 (A), SW3.1 (A), TP1.1, TP2.1, U8.1 (IN), U8.3 (EN), U37.4 (-)
/DRV1_ADC: C67.2, R103.2, TP55.1, U11.3 (CH2), U36.4
/DRV2_ADC: C68.2, R105.2, TP56.1, U11.2 (CH1), U36.3
/DRV3_ADC: C69.2, R107.2, TP57.1, U11.1 (CH0), U36.1
/DRV4_ADC: C71.2, R109.2, TP58.1, U11.4 (CH3), U36.6
/Drivers/DRV1_CTL: J7.35, R83.1, R84.1
/Drivers/DRV1_NEG: J9.2, R102.2, U34.3 (+)
/Drivers/DRV2_CTL: J7.33, R87.1, R88.1
/Drivers/DRV2_NEG: J9.4, R104.2, U35.2 (IN1+)
/Drivers/DRV3_CTL: J7.31, R91.1, R92.1
/Drivers/DRV3_NEG: J9.6, R106.2, U35.5 (IN2+)
/Drivers/DRV4_CTL: J7.15, R100.1, R101.1
/Drivers/DRV4_NEG: J9.8, R108.2, U35.10 (IN3+)
/Drivers/DRV5_ADC: C72.2, R111.2, TP59.1, U38.3 (CH2), U39.6
/Drivers/DRV5_CTL: J7.13, R114.1, R115.1
/Drivers/DRV5_NEG: J9.10, R110.2, U35.12 (IN4+)
/Drivers/IGN_CONT: J7.40, R14.2, R15.1
/Drivers/IGN_CTL: J7.11, R16.1, R17.1
/Drivers/IGN_NEG: J11.3, Q3.2 (D), R13.2, R14.1
/Drivers/IGN_POS: D7.2 (A), D8.2 (A), F2.2, J10.1, J10.2, J11.2, J12.1
/Drivers/MOS1: D11.2 (A), Q4.2 (D), R82.2, R102.1, U34.4 (-)
/Drivers/MOS2: D14.2 (A), Q5.2 (D), R86.2, R104.1, U35.3 (IN1-)
/Drivers/MOS3: D17.2 (A), Q6.2 (D), R90.2, R106.1, U35.6 (IN2-)
/Drivers/MOS4: D20.2 (A), Q7.2 (D), R99.2, R108.1, U35.9 (IN3-)
/Drivers/MOS5: D23.2 (A), Q8.2 (D), R110.1, R113.2, U35.13 (IN4-)
/Drivers/driver_nmos1/DRV_POS: D12.2 (A), D13.2 (A), D14.1 (K), F4.2, J9.3
/Drivers/driver_nmos2/DRV_POS: D15.2 (A), D16.2 (A), D17.1 (K), F5.2, J9.5
/Drivers/driver_nmos3/DRV_POS: D18.2 (A), D19.2 (A), D20.1 (K), F6.2, J9.7
/Drivers/driver_nmos4/DRV_POS: D21.2 (A), D22.2 (A), D23.1 (K), F7.2, J9.9
/Drivers/driver_nmos/DRV_POS: D9.2 (A), D10.2 (A), D11.1 (K), F3.2, J9.1
/Load Cells/IN_AMP_VREF: RV1.2, U7.2 (-), U7.6 (-), U7.9 (-), U7.13 (-)
/Load Cells/LC_Amplification1/IN1: J4.6, R26.2, TP28.1, U2.3
/Load Cells/LC_Amplification1/IN2: J4.7, R29.2, TP32.1, U2.1
/Load Cells/LC_Amplification1/OUT: C22.1, TP7.1, TP30.1, U3.6 (CH5), U4.6, U6.6 (-), U6.7
/Load Cells/LC_Amplification2/IN1: R32.2, TP33.1, U5.6
/Load Cells/LC_Amplification2/IN2: R35.2, TP37.1, U5.4
/Load Cells/LC_Amplification2/OUT: C26.1, TP8.1, TP35.1, U3.7 (CH6), U4.1, U6.8, U6.9 (-)
/Load Cells/LC_Amplification3/IN1: R38.2, TP38.1, U5.3
/Load Cells/LC_Amplification3/IN2: R41.2, TP42.1, U5.1
/Load Cells/LC_Amplification3/OUT: C30.1, TP9.1, TP40.1, U3.8 (CH7), U4.3, U6.13 (-), U6.14
/Load Cells/LC_Amplification/IN1: J4.2, R20.2, TP23.1, U2.6
/Load Cells/LC_Amplification/IN2: J4.3, R23.2, TP27.1, U2.4
/Load Cells/LC_Amplification/OUT: C18.1, TP6.1, TP25.1, U3.5 (CH4), U4.4, U6.1, U6.2 (-)
/Load Cells/LC_CS: J7.22, U3.10 (~CS/SHDN)
/Load Cells/LC_SELECTOR: J7.16, U18.6, U20.6, U22.6, U24.6
/Load Cells/TC_1_ADC: Ce1.1, TP14.1, TP15.1, U3.3 (CH2), U15.1, U17.6 (-), U17.7
/Load Cells/TC_2_ADC: Ce2.1, TP16.1, TP17.1, U3.4 (CH3), U15.3, U17.1, U17.2 (-)
/Load Cells/TC_3_ADC: Ce3.1, TP18.1, TP19.1, U3.1 (CH0), U15.4, U17.13 (-), U17.14
/Load Cells/TC_4_ADC: Ce4.1, TP20.1, TP21.1, U3.2 (CH1), U15.6, U17.8, U17.9 (-)
/Pressure Transducers/CS: J7.26, U11.10 (~CS/SHDN)
/Pressure Transducers/pt_circuitry1/IN: R44.1, TP43.1, U10.10 (+)
/Pressure Transducers/pt_circuitry1/OUT: C34.1, R45.2, TP11.1, TP44.1, U9.8, U11.8 (CH7), U12.3
/Pressure Transducers/pt_circuitry2/IN: R49.1, TP45.1, U10.5 (+)
/Pressure Transducers/pt_circuitry2/OUT: C36.1, R50.2, TP12.1, TP46.1, U9.7, U11.5 (CH4), U12.4
/Pressure Transducers/pt_circuitry3/IN: R54.1, TP47.1, U10.3 (+)
/Pressure Transducers/pt_circuitry3/OUT: C38.1, R55.2, TP13.1, TP48.1, U9.1, U11.6 (CH5), U12.6
/Pressure Transducers/pt_circuitry/IN: R95.1, TP52.1, U10.12 (+)
/Pressure Transducers/pt_circuitry/OUT: C64.1, R96.2, TP10.1, TP53.1, U9.14, U11.7 (CH6), U12.1
/Raspberry Pi/ADC2_CS: J7.24, U38.8 (~CS/SHDN)
/Raspberry Pi/RTC_CS: J7.37, U13.14 (E)
/Raspberry Pi/RTC_IRQ: J7.38, R9.2, U13.12 (IRQ)
/Regulators/battery_monitoring/Battery+: D1.1 (K), R116.1, R118.1, U1.4 (IN), U1.5 (IN), U1.6 (IN), U37.3 (+)
/SPI.CLK: J7.23, U3.13 (CLK), U11.13 (CLK), U13.11 (SCL), U38.11 (CLK)
/SPI.MISO: J7.21, U3.12 (Dout), U11.12 (Dout), U13.13 (SDO), U38.10 (Dout)
/SPI.MOSI: J7.19, U3.11 (Din), U11.11 (Din), U13.10 (SDI), U38.9 (Din)
/thermocouples/thermocouple_amp1/IN_1: R63.1, U14.1
/thermocouples/thermocouple_amp1/IN_2: R66.1, R67.2, U14.3
/thermocouples/thermocouple_amp2/IN_1: R69.1, U16.4
/thermocouples/thermocouple_amp2/IN_2: R72.1, R73.2, U16.6
/thermocouples/thermocouple_amp3/IN_1: R75.1, U16.1
/thermocouples/thermocouple_amp3/IN_2: R78.1, R79.2, U16.3
/thermocouples/thermocouple_amp/IN_1: R57.1, U14.4
/thermocouples/thermocouple_amp/IN_2: R60.1, R61.2, U14.6
GND: C1.2, C2.2, C3.2, C4.1, C5.1, C6.1, C6.2, C7.1, C7.2, C8.1, C9.2, C10.2, C11.2, C12.1, C12.2, C13.1, C13.2, C14.2, C15.1, C16.1, C17.1, C17.2, C19.1, C20.1, C21.1, C23.1, C24.1, C25.1, C27.1, C28.1, C29.1, C31.1, C32.1, C33.1, C35.2, C37.2, C39.2, C40.1, C41.2, C43.2, C44.1, C45.1, C45.2, C46.1, C47.2, C49.2, C50.1, C51.1, C51.2, C52.1, C53.2, C55.2, C56.1, C57.1, C57.2, C58.1, C59.2, C61.2, C62.1, C63.1, C63.2, C65.2, C66.2, C67.1, C68.1, C69.1, C70.2, C71.1, C72.1, C73.2, C74.2, C75.1, C76.2, C77.1, C77.2, D6.1 (K), J1.2, J2.1, J3.5 (GND), J3.6 (Shield), J4.4, J4.8, J7.6, J7.9, J7.14, J7.25, J7.30, J7.34, J7.39, J11.4, J12.2, MD1.3 (1_GROUND), MD1.7 (2_GROUND), Q3.3 (S), Q4.3 (S), Q5.3 (S), Q6.3 (S), Q7.3 (S), Q8.3 (S), R1.2, R2.2, R3.2, R4.2, R5.2, R7.2, R11.1, R12.2, R15.2, R17.2, R44.2, R46.1, R49.2, R51.1, R54.2, R56.1, R61.1, R67.1, R73.1, R79.1, R81.2, R84.2, R85.2, R88.2, R89.2, R92.2, R95.2, R97.1, R98.2, R101.2, R112.2, R115.2, R119.2, RV1.1, TP3.1, U1.1 (GND), U1.2 (GND), U1.3 (GND), U1.7 (GND), U2.2, U3.9 (DGND), U3.14 (AGND), U4.2, U5.2, U6.11 (V-), U7.11 (V-), U8.2 (GND), U9.11 (V-), U10.11 (V-), U11.9 (DGND), U11.14 (AGND), U12.2, U13.2 (NF), U13.9 (VSS), U13.16 (NF), U14.2, U15.2, U16.2, U17.11 (V-), U18.2 (GND), U19.4 (-Vs), U20.2 (GND), U21.4 (-Vs), U22.2 (GND), U23.4 (-Vs), U24.2 (GND), U25.4 (-Vs), U26.3 (-Vs), U27.5 (A), U28.3 (-Vs), U29.5 (A), U30.3 (-Vs), U31.5 (A), U32.3 (-Vs), U33.5 (A), U34.2 (GND), U35.11 (GND), U36.2, U37.2 (GND), U38.7 (DGND), U38.12 (AGND), U39.2, U40.2 (V-)
unnamed: C18.2, R21.1, R22.2
unnamed: C22.2, R27.1, R28.2
unnamed: C26.2, R33.1, R34.2
unnamed: C30.2, R39.1, R40.2
unnamed: C34.2, R42.2, R43.1
unnamed: C36.2, R47.2, R48.1
unnamed: C38.2, R52.2, R53.1
unnamed: C64.2, R93.2, R94.1
unnamed: Ce1.2, R58.2, R59.1
unnamed: Ce2.2, R64.2, R65.1
unnamed: Ce3.2, R70.2, R71.1
unnamed: Ce4.2, R76.2, R77.1
unnamed: D1.2 (A), SW2.2 (B)
unnamed: D2.1 (K), R1.1
unnamed: D3.1 (K), R3.1
unnamed: D4.2 (A), J3.1 (VBUS), Q1.1 (D), TP5.1
unnamed: D4.1 (K), R5.1
unnamed: D6.2 (A), Q2.1 (E)
unnamed: D7.1 (K), R12.1
unnamed: D8.1 (K), R13.1
unnamed: D9.1 (K), R81.1
unnamed: D10.1 (K), R82.1
unnamed: D12.1 (K), R85.1
unnamed: D13.1 (K), R86.1
unnamed: D15.1 (K), R89.1
unnamed: D16.1 (K), R90.1
unnamed: D18.1 (K), R98.1
unnamed: D19.1 (K), R99.1
unnamed: D21.1 (K), R112.1
unnamed: D22.1 (K), R113.1
unnamed: J1.1, SW1.2 (B)
unnamed: F1.1, J2.2
unnamed: C10.1, R6.1, U8.5 (OUT)
unnamed: J7.3, R8.2, R11.2
unnamed: MD1.6 (TRIM), R4.1
unnamed: C1.1, MD1.2 (VIN), SW3.2 (B)
unnamed: Q2.2 (B), R8.1
unnamed: Q3.1 (G), R16.2, TP22.1
unnamed: Q4.1 (G), R83.2, TP49.1
unnamed: Q5.1 (G), R87.2, TP50.1
unnamed: Q6.1 (G), R91.2, TP51.1
unnamed: Q7.1 (G), R100.2, TP54.1
unnamed: Q8.1 (G), R114.2, TP60.1
unnamed: R18.2, U18.3
unnamed: R19.2, U18.1
unnamed: R24.2, U20.3
unnamed: R25.2, U20.1
unnamed: R30.2, U22.3
unnamed: R31.2, U22.1
unnamed: R36.2, U24.3
unnamed: R37.2, U24.1
unnamed: R103.1, U34.1
unnamed: R117.1, U37.1
unnamed: F1.2, SW2.1 (A)
unnamed: C21.2, R22.1, U6.3 (+)
unnamed: C25.2, R28.1, U6.5 (+)
unnamed: C29.2, R34.1, U6.10 (+)
unnamed: C33.2, R40.1, U6.12 (+)
unnamed: R6.2, R7.1, U8.4 (FB)
unnamed: C39.1, R53.2, U9.3 (+)
unnamed: R55.1, R56.2, U9.2 (-)
unnamed: C37.1, R48.2, U9.5 (+)
unnamed: R50.1, R51.2, U9.6 (-)
unnamed: C35.1, R43.2, U9.10 (+)
unnamed: R45.1, R46.2, U9.9 (-)
unnamed: C65.1, R94.2, U9.12 (+)
unnamed: R96.1, R97.2, U9.13 (-)
unnamed: R52.1, U10.1, U10.2 (-)
unnamed: R47.1, U10.6 (-), U10.7
unnamed: R42.1, U10.8, U10.9 (-)
unnamed: R93.1, U10.13 (-), U10.14
unnamed: R10.2, U13.5 (RST)
unnamed: C15.2, U13.8 (VBAT)
unnamed: C49.1, R65.2, U17.3 (+)
unnamed: C43.1, R59.2, U17.5 (+)
unnamed: C61.1, R77.2, U17.10 (+)
unnamed: C55.1, R71.2, U17.12 (+)
unnamed: R23.1, U19.3 (+IN)
unnamed: U18.4, U19.8 (+RG)
unnamed: R20.1, U19.2 (-IN)
unnamed: R21.2, TP24.1, U19.6 (OUT)
unnamed: TP26.1, U7.1, U7.3 (+), U19.5 (REF)
unnamed: R18.1, R19.1, U19.1 (Rg)
unnamed: R29.1, U21.3 (+IN)
unnamed: U20.4, U21.8 (+RG)
unnamed: R26.1, U21.2 (-IN)
unnamed: R27.2, TP29.1, U21.6 (OUT)
unnamed: TP31.1, U7.5 (+), U7.7, U21.5 (REF)
unnamed: R24.1, R25.1, U21.1 (Rg)
unnamed: R35.1, U23.3 (+IN)
unnamed: U22.4, U23.8 (+RG)
unnamed: R32.1, U23.2 (-IN)
unnamed: R33.2, TP34.1, U23.6 (OUT)
unnamed: TP36.1, U7.8, U7.10 (+), U23.5 (REF)
unnamed: R30.1, R31.1, U23.1 (Rg)
unnamed: R41.1, U25.3 (+IN)
unnamed: U24.4, U25.8 (+RG)
unnamed: R38.1, U25.2 (-IN)
unnamed: R39.2, TP39.1, U25.6 (OUT)
unnamed: TP41.1, U7.12 (+), U7.14, U25.5 (REF)
unnamed: R36.1, R37.1, U25.1 (Rg)
unnamed: C42.1, C44.2, R60.2, U26.8 (+IN)
unnamed: C41.1, C42.2, R57.2, U26.1 (-IN)
unnamed: R62.1, U26.2 (REF), U27.3 (C), U27.4 (REF)
unnamed: R58.1, U26.5 (SENSE), U26.6
unnamed: C48.1, C50.2, R66.2, U28.8 (+IN)
unnamed: C47.1, C48.2, R63.2, U28.1 (-IN)
unnamed: R68.1, U28.2 (REF), U29.3 (C), U29.4 (REF)
unnamed: R64.1, U28.5 (SENSE), U28.6
unnamed: C54.1, C56.2, R72.2, U30.8 (+IN)
unnamed: C53.1, C54.2, R69.2, U30.1 (-IN)
unnamed: R74.1, U30.2 (REF), U31.3 (C), U31.4 (REF)
unnamed: R70.1, U30.5 (SENSE), U30.6
unnamed: C60.1, C62.2, R78.2, U32.8 (+IN)
unnamed: C59.1, C60.2, R75.2, U32.1 (-IN)
unnamed: R80.1, U32.2 (REF), U33.3 (C), U33.4 (REF)
unnamed: R76.1, U32.5 (SENSE), U32.6
unnamed: R105.1, U35.1 (OUT1)
unnamed: R107.1, U35.7 (OUT2)
unnamed: R109.1, U35.8 (OUT3)
unnamed: R111.1, U35.14 (OUT4)
unnamed: C75.2, R117.2, TP61.1, U38.1 (CH0), U39.4
unnamed: TP62.1, U38.2 (CH1), U39.3, U40.1, U40.4 (-)
unnamed: R118.2, R119.1, U40.3 (+)

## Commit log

2024-09-30 modified sch
    [battery_monitoring.kicad_sch, curr_monitor.kicad_sch, driver_nmos.kicad_sch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]
2024-11-15 Version alpha
    [battery_monitoring.kicad_sch, curr_monitor.kicad_sch, driver_nmos.kicad_sch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]
2024-11-15 unrouted adc traces
    [karca_v2.kicad_pcb]
2024-11-18 quick fix
    [karca_v2.kicad_pcb]
2024-11-18 Checkpoint before ripping everything apart
    [karca_v2.kicad_pcb]
2024-11-19 Saved the 12V rail
    [karca_v2.kicad_pcb]
2024-11-19 rearrange regs
    [karca_v2.kicad_pcb]
2024-11-20 discrete traces
    [battery_monitoring.kicad_sch, curr_monitor.kicad_sch, driver_nmos.kicad_sch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]
2024-11-21 fixed TVS Diodes
    [battery_monitoring.kicad_sch, curr_monitor.kicad_sch, driver_nmos.kicad_sch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]
2024-11-23 vias pt 1
    [pt_amp.kicad_sch]
2024-11-23 fixed violations
    [battery_monitoring.kicad_sch, drivers.kicad_sch, regulators.kicad_sch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]
2024-11-23 stitching capacitors for SPI signals
2024-11-27 Fixed ground capacitors
    [battery_monitoring.kicad_sch, curr_monitor.kicad_sch, driver_nmos.kicad_sch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]
2024-11-27 Fixed silkscreen
2024-11-29 save before rerouting
    [regulators.kicad_sch]
2024-12-01 pin 1 labels and straight traces to IC pads
2024-12-01 fixed pmos
    [regulators.kicad_sch]
2024-12-02 replaced digital switches with jumpers, simpler design
    [karca_v2.kicad_sch, lc_amp.kicad_sch, load_cells.kicad_sch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]
2024-12-03 Passed all DRC, Added safety jumper to isolate regulators from rest of the board
    [battery_monitoring.kicad_sch, curr_monitor.kicad_sch, driver_nmos.kicad_sch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]
2024-12-15 changed capacitor values and sizes for production
    [karca_v2-B_Mask.gbr, karca_v2-B_Paste.gbr, karca_v2-B_S2.gbr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]
2024-12-27 cleaned up documentation. Added production files and BOM. Marked Thermocouple components and THT components as DNP (excluded them from BOM too) to match version sent to JLCPCB for fabrication
    [battery_monitoring.kicad_sch, curr_monitor.kicad_sch, driver_nmos.kicad_sch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]
2024-12-28 added changelog
    [kARCA_v2_Changelog.csv]
2024-12-28 added board files
    [kARCA_v2_Changelog.csv, karca_v2_BOM.csv]
2025-01-04 BOM of THT added
    [BOM_with_THT_components.csv, kARCA_v2_Changelog.csv]
2025-01-24 updated THT BOM
    [BOM_with_THT_components.csv, regulators.kicad_sch]
2025-05-25 revisions for V2.1
    [battery_monitoring.kicad_sch, curr_monitor.kicad_sch, driver_nmos.kicad_sch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]
2025-05-25 added production files
    [karca_v2-B_Mask.gbs, karca_v2-B_Paste.gbp, karca_v2-B_S2.gbl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]
2025-05-25 updated BOM
    [karca_v2_BOM.csv]
2025-05-25 updated POS
    [karca_v2_BOM.csv, raspberry_pi.kicad_sch, regulators.kicad_sch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]
2025-06-17 saving changes
    [karca_v2-top-pos.csv]
2025-09-20 Replaced header with a smaller one, added silksreen labels, and removed secondary USB power source
    [battery_monitoring.kicad_sch, curr_monitor.kicad_sch, driver_nmos.kicad_sch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]
2025-09-23 changed pin header to a smaller one and removed USB secondary power supply
    [karca_v2_testing.xlsx, regulators.kicad_sch]
2026-03-21 re-added sims and gerbers
    [karca_v2-B_Mask.gbs, karca_v2-B_Paste.gbp, karca_v2-B_S2.gbl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]
2026-03-23 reorganized ADCs
    [battery_monitoring.kicad_sch, curr_monitor.kicad_sch, driver_nmos.kicad_sch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]
2026-03-24 finished schematic for v2.1
    [battery_monitoring.kicad_sch, curr_monitor.kicad_sch, driver_nmos.kicad_sch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]
2026-03-25 swapped adcs
    [battery_monitoring.kicad_sch, curr_monitor.kicad_sch, driver_nmos.kicad_sch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]
2026-03-25 added precision shunt reference to ADCs and second SPI bus for driver current and battery voltage monitors
    [battery_monitoring.kicad_sch, karca_v2.kicad_sch, lc_amp.kicad_sch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]
2026-03-25 Swapped IRF3708 FETs for AO3400 for more compact package
    [driver_nmos.kicad_sch, drivers.kicad_sch, pt_amp.kicad_sch]
2026-03-27 All tests passed. Going to run DFM next
    [battery_monitoring.kicad_sch, curr_monitor.kicad_sch, driver_nmos.kicad_sch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]
2026-03-28 changed diode to SMD schottky and fixed switches
    [regulators.kicad_sch]
2026-03-28 fixed all routing. Now need to clean up vias
    [battery_monitoring.kicad_sch, curr_monitor.kicad_sch, drivers.kicad_sch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]
2026-03-28 via array completed. Time for gerbers and bom
2026-03-29 final production version
    [battery_monitoring.kicad_sch, bom.csv, curr_monitor.kicad_sch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]
2026-05-24 fixed changelog
    [kARCA_v2_Changelog.csv]
2026-05-24 removed extraneous files
    updated gitignore to remove extraneous files
    removed unnecessary files
    updated gitignore to remove extraneous files
    removed extra spice sims
    removed all extra files
    [battery_monitoring.kicad_sch, curr_monitor.kicad_sch, driver_nmos.kicad_sch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]
